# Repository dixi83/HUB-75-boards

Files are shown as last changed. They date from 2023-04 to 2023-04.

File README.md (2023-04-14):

# HUB-75 boards

The HUB-75 boards is a collection of break-out boards (BOBs) for HUB-75 connnectors found on re-purposed FPGA cards such as the 5A-75B and 5A-75E. These cards can be picked up for 10\~20 dollars from China and form an ideal basis for tinkering with FPGAs. Based on these cheap FPGA's a project has been spraked, called Litex-CNC, which aims to repurpose these cards to a cheap CNC controller. CNC-machines normally have field power which is 12\~24V and thus the FPGA cannot direclty be connected to the components of the machine. Therefore a set of break-out boards have been developed for GPIO inputs/outputs, stepgen, encoders, etc.

## Design philosophy
> Why not a hat one might ask? This project offers more flexibility. By combining different break-out can be combined to suit the machine that is being built. A hat also comes with a larger risk in design errors; smaller boards are easier to design, produce and check.

All BOBs will have the same dimensions of 85 mm x 56 mm. This size is equal to that of the Raspberry Pi 4, however the mounting holes are placed on the four corners and thus different from the RPi. Getting the mounting holes at the same location as the RPi made the design much more difficult. Placement of the connectors also hampers stacking these boards on top of each other, so not being to able to stack them on top of a RPi seems permissible.

The outputs of the BOBs will be on the bottom edge (long side). Field power and logic power are provided from the left side of the board. The HUB-75 connectors will be placed on the top of the boards. This makes it easier to route the digital signals and high-power signals separately from each other in the cabinet.

The smalles trace and spacing is 0.2 mm. These boards are designed to be ordered from an online PCB manufacturer. Some desktop milling machines might have the accuracy to create these traces, so you might give it a try when you are feeling lucky. The smallest holes (vias) are 0.3 mm in size.

All components are selected to be hand-solderable. This means that the following minimum sizes SMD components will be used:
- resistors, LED's, capacitors: SMD-1206
- diodes: SOD-123
- FET, transistors: SOT-23

## HUB-75 pinout
Each connector has 6 individual pins (1, 2, 3, 5, 6, and 7) and 8 shared pins (8 through 15). The standard pin-out of a HUB-75 connector is shown below.

| HUB75 pin | Pin | Pin | HUB75 pin |
|---|---|---|---|
| R0 | 1 | 2 | G0 |
| B0 | 3 | 4 | *GND* |
| R1 | 5 | 6 | G1 |
| B1 | 7 | 8 | E |
| A | 9 | 10 | B |
| C | 11 | 12 | D |
| CLK | 13 | 14 | STB |
| OE | 15 | 16 | *GND* |

Each HUB-75 connector will use the individual pins and in special cases one of the shared pins. In the design it should be taken into account that boards which uses the same shared pins might be mutual exclusive when the functions are different (different types of stepgen BOBs can off course be combined.

## Available BOBs
The table below shows the BOBs which are currently available in this repository, along with their status.

| Category  | Name | Description | HUB-75 | Status |
|---|---|---|---|---|
| stepgen | [HUB75-Differential_stepgen](HUB75-Differential_stepgen) | 3 differential stepgen channels, frequency up to 400 kHz | 2 + 0.5 | Prototype-2 ordered |
| GPIO-out  | [HUB75-Sourcing_output](HUB75-Sourcing_output) | 12 channel sourcing output (<1 kHz, 4 A per channel, 4 A total) | 2 | Prototype-2 ordered |
| GPIO-in | [HUB75-Sinking_input](HUB75-Sinking_input) | 12 channel sinking input (< 1 kHz) | 2 | Untested |
| GPIO-in | [HUB75-Sinking_input_screw_terminals](HUB75-Sinking_input_screw_terminals)  | 6 channel sinking input with screw terminals (< 1 kHz) | 2 | Untested |

## Connecting the BOBs to your FPGA
On both the 5A-75B and the 5A-75E the `74HC245T` buffers are hard-wired as outputs. To be able to use the HUB-75 boards which require an input (as seen from the FPGA) some modifications on the board are required. Of both boards different versiosn exist, so the components can be at a different location on your board. Below are the locations of the buffer on a 5A-75B V6.1 (front) and 5A-75E V6.0 (back).

5A-75B V6.1

5A-75E V6.0

Each buffer has 8 channels, while every HUB-75 connector has 6 individual pins. When you replace a buffer you will cahnge the behavior of one HUB-75 connector and partly that of its neighbor. All HUB-75 boards assume that a connector is either fully configured as input or as output. Therefore it is recommended to change the buffers direclty adjacent to each other, so the minimum amount of available connectors (partly input/ouput) are wasted.

The following changes have to be made to the buffers:
* De-solder the `74HC245T` buffer, this buffer cannot be re-used because its pins are not 5 Volt tolerant when `Vcc` is 3.3 Volt.
* Cut the trace to the pin `Vcc` (pin 20) and wire it to a 3.3V source (for example the JTAG-header). If you don't do this, a buffer configure as input will put 5 Volts on the pins of the FPGA, which will definately fry that pin or the whole board.
* Cut the trace to the pin `DIR` (pin 1) and wire it to a GND source to configure the buffer as input.
* Replace the buffer with a buffer with 5V tolerant inputs, such as the `74LVC245` ([datasheet](https://www.ti.com/lit/ds/symlink/sn74lvc245a.pdf)).

After these modifications the board might look a like this (on this particular board a single buffer has been replace, as it is a test-board for LitexCNC).

TODO: picture to be taken

## License 
The boards in this repository are licensed unde Creative Commons BY-NC-SA. This means you are allowed to:
* **Share** — copy and redistribute the material in any medium or format
* **Adapt** — remix, transform, and build upon the material

As long as:
* **Attribution** — You must give appropriate credit, provide a link to the license, and indicate if changes were made. You may do so in any reasonable manner, but not in any way that suggests the licensor endorses you or your use.
* **NonCommercial** — You may not use the material for  commercial purposes. Of course you can use the machine you created or modified using these boards for commercial purposes. 
* **ShareAlike** — If you remix, transform, or build upon the material, you must distribute your contributions under the  same license  as the original.

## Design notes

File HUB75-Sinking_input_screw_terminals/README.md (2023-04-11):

# HUB-75 Sinking input screw terminals
Break-out board with 6 channel sinking input. The FPGA is galvanically separated from field power using opto-couplers.

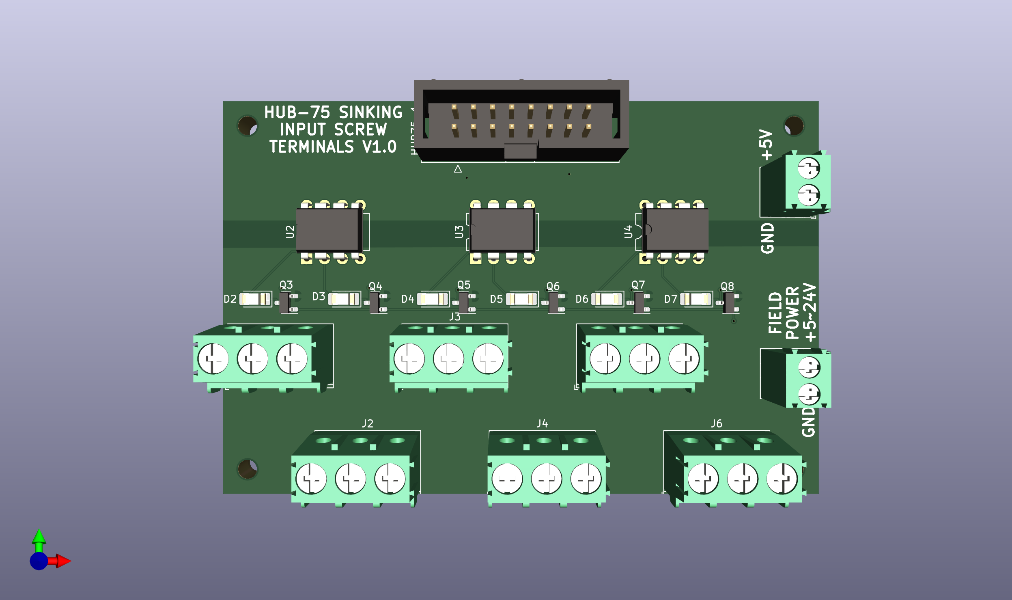
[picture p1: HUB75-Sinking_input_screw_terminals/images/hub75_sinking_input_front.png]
PCB front


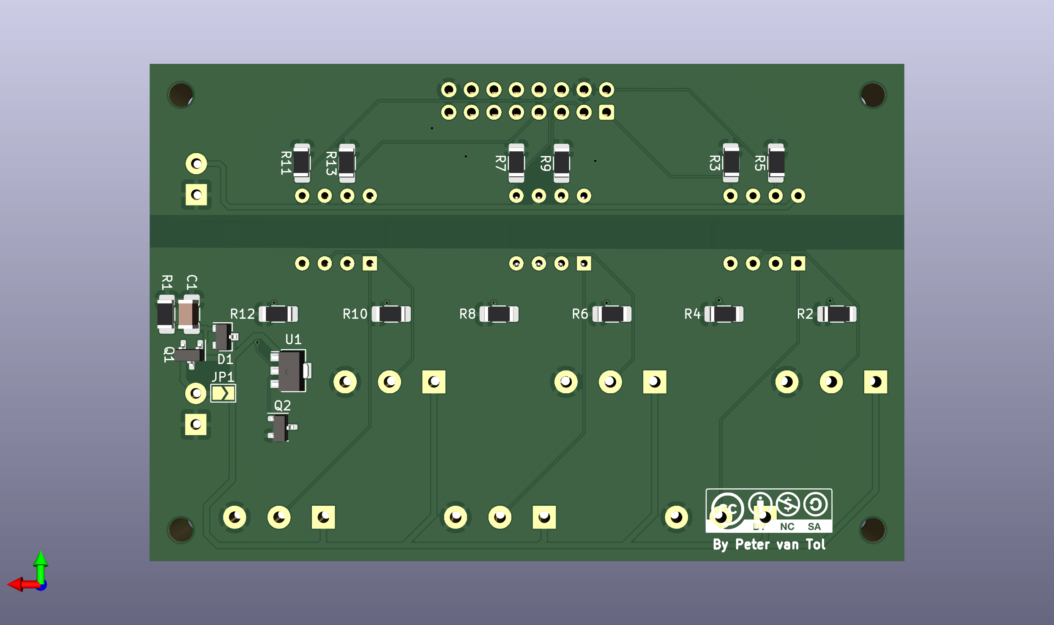
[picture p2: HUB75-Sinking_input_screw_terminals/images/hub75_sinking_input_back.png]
PCB back


## Features

- 1 HUB-75 output connector
- 6 channel sinking output using screw terminals
- 5\~24 V Field power with reverse polarity protection
- indicating LED for each output
- indicated switching frequency 1 kHz

## Applications

- PNP (souring) limit switches
- Momentary push-buttons
- Slow encoders, for example for user input

> **NOTE** <br> The `PC827` optocouplers have a maximum rated frequency of 80 kHz. It is recommended to start at a frequency of 1 kHz and work up from there.

## Example wiring

TODO: example

## Litex-CNC example configuration
Let's assume that the two HUB-745 connectors on this board are connected to J15 and J16 of the FPGA. To configure the pins for output, you can use the configuration-block below as a starting point. Optionaly the pin names can also be set in the configuration, making the HAL clearer.

``` json
{
    ...,
    "gpio_in": [
        {"pin": "j15:0"},
        {"pin": "j15:1"},
        {"pin": "j15:2"},
        {"pin": "j15:4"},
        {"pin": "j15:5"},
        {"pin": "j15:6"}
    ],
    ...
}
```

Alternatively, the BOB can also be used for PWM output. In that case the configuration may look something like below. In this example it is assumed that outputs on J16 are used for three encoders.

``` json
{
    ...,
    "encoders": [
        {  
            "pin_A":"j16:0",
            "pin_B":"j16:1"
        },
        {  
            "pin_A":"j16:2",
            "pin_B":"j16:4"
        },
        {  
            "pin_A":"j16:5",
            "pin_B":"j16:6"
        }
    ],
    ...
}
```

## Bill of materials

The table below gives the bill of materials used for this BOB and an indication of its price. The list is available as public list for the following companies:
* [Reichtelt](https://www.reichelt.de/my/1998173). This is non-affiliate link, I do not earn any money when you order this list from this specific vendor, nor the vendor endorses this project. Reichtelt is a supplyer for Western Europe.

When you order with Mouser or antohter supplier, please share a list here.

| Part. number | Package | Description | Datasheet | Amount | Price*  |
|---|---|---|---|---|---|
| LTV827 | DIP-8 | Dual-channel opto-coupler | | 3 | € 0.31  |
| AO3401A | SOT-23 | P-Channel MOSFET, 30V | | 1 | € 0.25  |
| ZENER 12V | SOT-23 | 12V Zener diode*** | | 1 | € 0.05  |
| 4.7K | SMD 1206  | Resistor, 4.7 kOhm | | 6 | € 0.03  |
| 10K | SMD 1206  | Resistor, 10 kOhm | | 1 | € 0.03  |
| LED | SMD 1206  | LED, green, If > 20 mA | | 6 | € 0.08  |
| CAP 15N | SMD 1206  | Capitor, 15 nF | | 1 | € 0.02  |
| Phoenix_PT-1,5-3-5.0  | - | JST XH conn. 2.5 mm pitch | | 6 | € 0.15  |
| Phoenix_PT-1,5-2-3.5  | - | Screw/spring terminal 2.5 mm pitch | | 2 | € 0.22  |
| BOX 2X8 | - | Box header 2x8, 2.54 mm pitch | | 2 | € 0.16  |
| 2N7002** | SOT-23 | N-Channel MOSFET (current mirror)  | | 7 | € 0.04  |
| CL2N8-G** | SOT-89 | LED-driver 20 mA (current mirror)  | | 1 | € 0.39  |
| R** | SMD 1206  | Resistor, TBD Ohm (alternative) | | 6 | € 0.03  |

**NOTES**: 
1. The price is based on availability in the Netherlands with a single shop for all parts. Parts might be sourced cheaper depending on your location, available sources and the time you want to wait before receiving the components.
2. The components `CL2N8-G` and `2N7002` form a current mirror for driving the status LEDs. This current mirror can be replaced with a fixed resistor `R`, which should be calculated based on the voltage used for Field power.
3. The zener diode is only required when Field Power is >12 Volt for protecting the MOSFETs.

## Known issues

This board does not have any known issues yet.

If you find any issue, please file a bug using GitHub.

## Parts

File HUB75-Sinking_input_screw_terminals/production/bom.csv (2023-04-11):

Source: | C:\Users\Martijn Diks\OneDrive\Documenten\documents\Projects\RatRig Killerbee\ControllerBoard\BOBs\HUB-75-boards-main\HUB75-Sinking_input_screw_terminals\kicad\HUB75-Sinking_input.kicad_sch
Date: | 11-4-2023 18:23:18
Tool: | Eeschema (6.0.9)
Generator: | C:\Program Files\KiCad\6.0\bin\scripting\plugins/bom_csv_grouped_by_value.py
Component Count: | 43
Individual Components:
Item | Qty | Reference(s) | Value | LibPart | Footprint | Datasheet
 |  | C1 | 15nF | Device:C | Capacitor_SMD:C_1206_3216Metric_Pad1.33x1.80mm_HandSolder | ~
 |  | D1 | D_Zener | Device:D_Zener | Diode_SMD:D_SOT-23_ANK | ~
 |  | D2 | LED_Small | Device:LED_Small | LED_SMD:LED_1206_3216Metric_Pad1.42x1.75mm_HandSolder | ~
 |  | D3 | LED_Small | Device:LED_Small | LED_SMD:LED_1206_3216Metric_Pad1.42x1.75mm_HandSolder | ~
 |  | D4 | LED_Small | Device:LED_Small | LED_SMD:LED_1206_3216Metric_Pad1.42x1.75mm_HandSolder | ~
 |  | D5 | LED_Small | Device:LED_Small | LED_SMD:LED_1206_3216Metric_Pad1.42x1.75mm_HandSolder | ~
 |  | D6 | LED_Small | Device:LED_Small | LED_SMD:LED_1206_3216Metric_Pad1.42x1.75mm_HandSolder | ~
 |  | D7 | LED_Small | Device:LED_Small | LED_SMD:LED_1206_3216Metric_Pad1.42x1.75mm_HandSolder | ~
 |  | HUB75-1 | Conn_02x08_Odd_Even | Connector_Generic:Conn_02x08_Odd_Even | Connector_IDC:IDC-Header_2x08_P2.54mm_Vertical | ~
 |  | J1 | Conn_01x03_Male | Connector:Conn_01x03_Male | Connector_JST:JST_XH_B3B-XH-A_1x03_P2.50mm_Vertical | ~
 |  | J2 | Conn_01x03_Male | Connector:Conn_01x03_Male | Connector_JST:JST_XH_B3B-XH-A_1x03_P2.50mm_Vertical | ~
 |  | J3 | Conn_01x03_Male | Connector:Conn_01x03_Male | Connector_JST:JST_XH_B3B-XH-A_1x03_P2.50mm_Vertical | ~
 |  | J4 | Conn_01x03_Male | Connector:Conn_01x03_Male | Connector_JST:JST_XH_B3B-XH-A_1x03_P2.50mm_Vertical | ~
 |  | J5 | Conn_01x03_Male | Connector:Conn_01x03_Male | Connector_JST:JST_XH_B3B-XH-A_1x03_P2.50mm_Vertical | ~
 |  | J6 | Conn_01x03_Male | Connector:Conn_01x03_Male | Connector_JST:JST_XH_B3B-XH-A_1x03_P2.50mm_Vertical | ~
 |  | JP1 | Jumper_2_Open | Jumper:Jumper_2_Open | Jumper:SolderJumper-2_P1.3mm_Open_TrianglePad1.0x1.5mm | ~
 |  | PWR1 | Screw_Terminal_01x02 | Connector:Screw_Terminal_01x02 | TerminalBlock_Phoenix:TerminalBlock_Phoenix_PT-1,5-2-3.5-H_1x02_P3.50mm_Horizontal | ~
 |  | PWR2 | Screw_Terminal_01x02 | Connector:Screw_Terminal_01x02 | TerminalBlock_Phoenix:TerminalBlock_Phoenix_PT-1,5-2-3.5-H_1x02_P3.50mm_Horizontal | ~
 |  | Q1 | AO3401A | Transistor_FET:AO3401A | Package_TO_SOT_SMD:SOT-23 | http://www.aosmd.com/pdfs/datasheet/AO3401A.pdf
 |  | Q2 | 2N7002 | Transistor_FET:2N7002 | Package_TO_SOT_SMD:SOT-23 | https://www.onsemi.com/pub/Collateral/NDS7002A-D.PDF
 |  | Q3 | 2N7002 | Transistor_FET:2N7002 | Package_TO_SOT_SMD:SOT-23 | https://www.onsemi.com/pub/Collateral/NDS7002A-D.PDF
 |  | Q4 | 2N7002 | Transistor_FET:2N7002 | Package_TO_SOT_SMD:SOT-23 | https://www.onsemi.com/pub/Collateral/NDS7002A-D.PDF
 |  | Q5 | 2N7002 | Transistor_FET:2N7002 | Package_TO_SOT_SMD:SOT-23 | https://www.onsemi.com/pub/Collateral/NDS7002A-D.PDF
 |  | Q6 | 2N7002 | Transistor_FET:2N7002 | Package_TO_SOT_SMD:SOT-23 | https://www.onsemi.com/pub/Collateral/NDS7002A-D.PDF
 |  | Q7 | 2N7002 | Transistor_FET:2N7002 | Package_TO_SOT_SMD:SOT-23 | https://www.onsemi.com/pub/Collateral/NDS7002A-D.PDF
 |  | Q8 | 2N7002 | Transistor_FET:2N7002 | Package_TO_SOT_SMD:SOT-23 | https://www.onsemi.com/pub/Collateral/NDS7002A-D.PDF
 |  | R1 | 10K | Device:R | Resistor_SMD:R_1206_3216Metric_Pad1.30x1.75mm_HandSolder | ~
 |  | R2 | R | Device:R | Resistor_SMD:R_1206_3216Metric_Pad1.30x1.75mm_HandSolder | ~
 |  | R3 | 4.7K | Device:R | Resistor_SMD:R_1206_3216Metric_Pad1.30x1.75mm_HandSolder | ~
 |  | R4 | R | Device:R | Resistor_SMD:R_1206_3216Metric_Pad1.30x1.75mm_HandSolder | ~
 |  | R5 | 4.7K | Device:R | Resistor_SMD:R_1206_3216Metric_Pad1.30x1.75mm_HandSolder | ~
 |  | R6 | R | Device:R | Resistor_SMD:R_1206_3216Metric_Pad1.30x1.75mm_HandSolder | ~
 |  | R7 | 4.7K | Device:R | Resistor_SMD:R_1206_3216Metric_Pad1.30x1.75mm_HandSolder | ~
 |  | R8 | R | Device:R | Resistor_SMD:R_1206_3216Metric_Pad1.30x1.75mm_HandSolder | ~
 |  | R9 | 4.7K | Device:R | Resistor_SMD:R_1206_3216Metric_Pad1.30x1.75mm_HandSolder | ~
 |  | R10 | R | Device:R | Resistor_SMD:R_1206_3216Metric_Pad1.30x1.75mm_HandSolder | ~
 |  | R11 | 4.7K | Device:R | Resistor_SMD:R_1206_3216Metric_Pad1.30x1.75mm_HandSolder | ~
 |  | R12 | R | Device:R | Resistor_SMD:R_1206_3216Metric_Pad1.30x1.75mm_HandSolder | ~
 |  | R13 | 4.7K | Device:R | Resistor_SMD:R_1206_3216Metric_Pad1.30x1.75mm_HandSolder | ~
 |  | U1 | CL2N8-G | Driver_LED:HV9921N8-G | Package_TO_SOT_SMD:SOT-89-3 | https://cdn-reichelt.de/documents/datenblatt/A200/CL2_DS.pdf
 |  | U2 | LTV-827 | Isolator:LTV-827 | Package_DIP:DIP-8_W7.62mm | http://optoelectronics.liteon.com/upload/download/DS-70-96-0016/LTV-8X7%20series%20201610%20.pdf
 |  | U3 | LTV-827 | Isolator:LTV-827 | Package_DIP:DIP-8_W7.62mm | http://optoelectronics.liteon.com/upload/download/DS-70-96-0016/LTV-8X7%20series%20201610%20.pdf
 |  | U4 | LTV-827 | Isolator:LTV-827 | Package_DIP:DIP-8_W7.62mm | http://optoelectronics.liteon.com/upload/download/DS-70-96-0016/LTV-8X7%20series%20201610%20.pdf
Collated Components:
Item | Qty | Reference(s) | Value | LibPart | Footprint | Datasheet
1 | 1 | C1 | 15nF | Device:C | Capacitor_SMD:C_1206_3216Metric_Pad1.33x1.80mm_HandSolder | ~
2 | 1 | D1 | D_Zener | Device:D_Zener | Diode_SMD:D_SOT-23_ANK | ~
3 | 6 | D2, D3, D4, D5, D6, D7 | LED_Small | Device:LED_Small | LED_SMD:LED_1206_3216Metric_Pad1.42x1.75mm_HandSolder | ~
4 | 1 | HUB75-1 | Conn_02x08_Odd_Even | Connector_Generic:Conn_02x08_Odd_Even | Connector_IDC:IDC-Header_2x08_P2.54mm_Vertical | ~
5 | 6 | J1, J2, J3, J4, J5, J6 | Conn_01x03_Male | Connector:Conn_01x03_Male | Connector_JST:JST_XH_B3B-XH-A_1x03_P2.50mm_Vertical | ~
6 | 1 | JP1 | Jumper_2_Open | Jumper:Jumper_2_Open | Jumper:SolderJumper-2_P1.3mm_Open_TrianglePad1.0x1.5mm | ~
7 | 2 | PWR1, PWR2 | Screw_Terminal_01x02 | Connector:Screw_Terminal_01x02 | TerminalBlock_Phoenix:TerminalBlock_Phoenix_PT-1,5-2-3.5-H_1x02_P3.50mm_Horizontal | ~
8 | 1 | Q1 | AO3401A | Transistor_FET:AO3401A | Package_TO_SOT_SMD:SOT-23 | http://www.aosmd.com/pdfs/datasheet/AO3401A.pdf
9 | 7 | Q2, Q3, Q4, Q5, Q6, Q7, Q8 | 2N7002 | Transistor_FET:2N7002 | Package_TO_SOT_SMD:SOT-23 | https://www.onsemi.com/pub/Collateral/NDS7002A-D.PDF
10 | 1 | R1 | 10K | Device:R | Resistor_SMD:R_1206_3216Metric_Pad1.30x1.75mm_HandSolder | ~
11 | 6 | R2, R4, R6, R8, R10, R12 | R | Device:R | Resistor_SMD:R_1206_3216Metric_Pad1.30x1.75mm_HandSolder | ~
12 | 6 | R3, R5, R7, R9, R11, R13 | 4.7K | Device:R | Resistor_SMD:R_1206_3216Metric_Pad1.30x1.75mm_HandSolder | ~
13 | 1 | U1 | CL2N8-G | Driver_LED:HV9921N8-G | Package_TO_SOT_SMD:SOT-89-3 | https://cdn-reichelt.de/documents/datenblatt/A200/CL2_DS.pdf
14 | 3 | U2, U3, U4 | LTV-827 | Isolator:LTV-827 | Package_DIP:DIP-8_W7.62mm | http://optoelectronics.liteon.com/upload/download/DS-70-96-0016/LTV-8X7%20series%20201610%20.pdf

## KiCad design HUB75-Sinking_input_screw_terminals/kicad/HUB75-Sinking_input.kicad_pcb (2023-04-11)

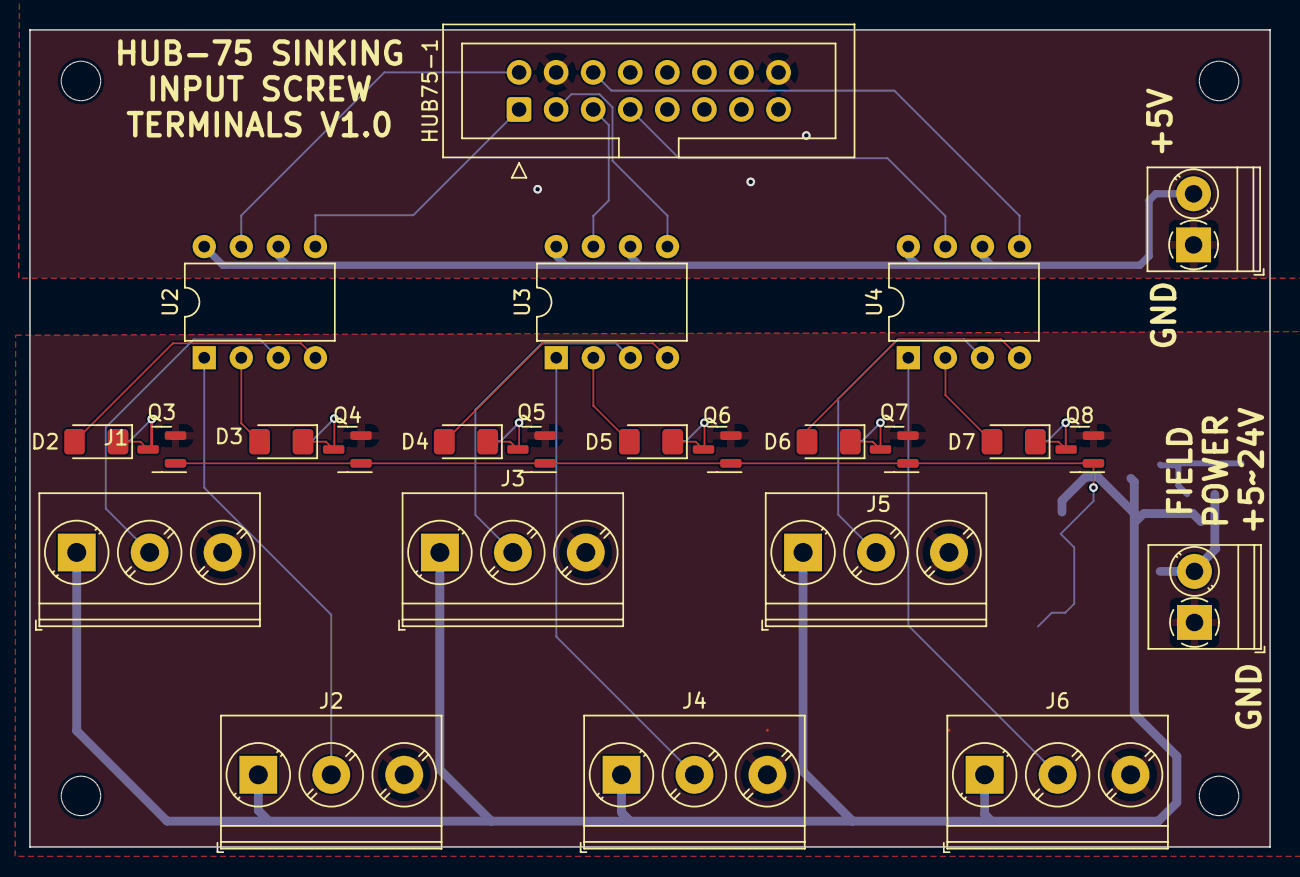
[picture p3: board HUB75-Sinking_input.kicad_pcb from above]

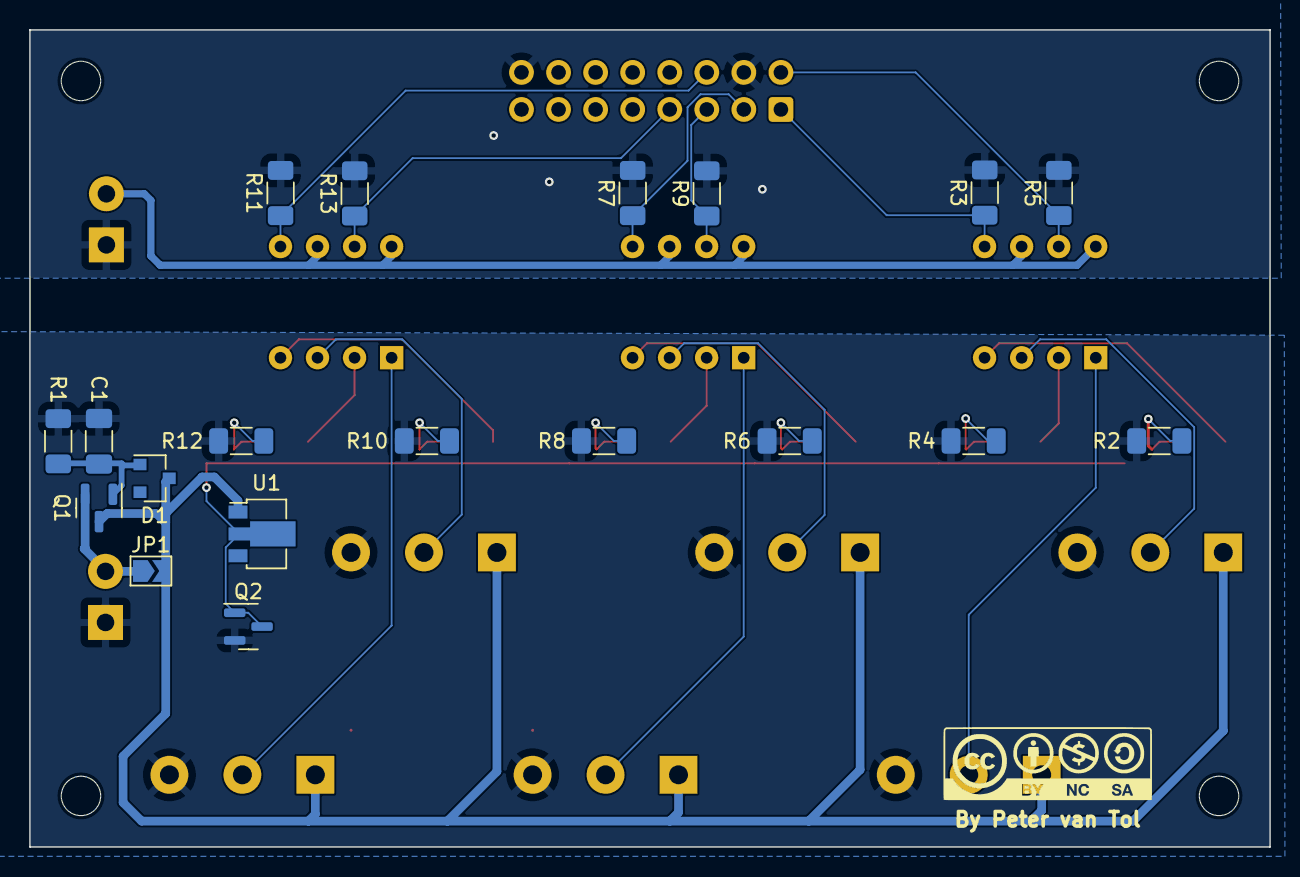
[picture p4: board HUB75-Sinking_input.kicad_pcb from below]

Board: 2 copper layers, 85.0 x 56.0 mm, 47 parts (19 on the bottom side), 31 nets.

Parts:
C1: 15nF; C_1206_3216Metric_Pad1.33x1.80mm_HandSolder
D1: D_Zener; D_SOT-23_ANK
D2, D3, D4, D5, D6, D7: LED_Small; LED_1206_3216Metric_Pad1.42x1.75mm_HandSolder
HOLE1, HOLE2, HOLE3, HOLE4: MountingHole_2.7mm_M2.5_DIN965
HUB75-1: Conn_02x08_Odd_Even; IDC-Header_2x08_P2.54mm_Vertical
J1, J2, J3, J4, J5: Conn_01x03_Male; TerminalBlock_Phoenix_PT-1,5-3-5.0-H_1x03_P5.00mm_Horizontal
J6: TerminalBlock_Phoenix:TerminalBlock_Phoenix_PT-1,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; TerminalBlock_Phoenix_PT-1,5-3-5.0-H_1x03_P5.00mm_Horizontal
JP1: Jumper_2_Open; SolderJumper-2_P1.3mm_Open_TrianglePad1.0x1.5mm
PWR1, PWR2: Screw_Terminal_01x02; TerminalBlock_Phoenix_PT-1,5-2-3.5-H_1x02_P3.50mm_Horizontal
Q1: AO3401A; SOT-23
Q2, Q3, Q4, Q5, Q6, Q7, Q8: 2N7002; SOT-23
R1: 10K; R_1206_3216Metric_Pad1.30x1.75mm_HandSolder
R2, R4, R6, R8, R10, R12: R; R_1206_3216Metric_Pad1.30x1.75mm_HandSolder
R3, R5, R7, R9, R11, R13: 4.7K; R_1206_3216Metric_Pad1.30x1.75mm_HandSolder
U1: CL2N8-G; SOT-89-3
U2, U3, U4: LTV-827; DIP-8_W7.62mm

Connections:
+5V: PWR2.2, U2.6, U2.8, U3.6, U3.8, U4.6, U4.8
CUR_MIRROR: Q2.1 (G), Q2.3 (D), Q3.1 (G), Q4.1 (G), Q5.1 (G), Q6.1 (G), Q7.1 (G), Q8.1 (G), U1.2 (GND)
GND: HUB75-1.4, HUB75-1.16, PWR2.1, R3.2, R5.2, R7.2, R9.2, R11.2, R13.2
GNDD: C1.2, J1.3, J2.3, J3.3, J4.3, J5.3, J6.3, PWR1.1, Q2.2 (S), Q3.2 (S), Q4.2 (S), Q5.2 (S), Q6.2 (S), Q7.2 (S), Q8.2 (S), R1.2, R2.1, R4.1, R6.1, R8.1, R10.1, R12.1
GPIO1-1: HUB75-1.1, R3.1, U2.5
GPIO1-2: HUB75-1.2, R5.1, U2.7
GPIO1-3: HUB75-1.3, R7.1, U3.5
GPIO1-4: HUB75-1.5, R9.1, U3.7
GPIO1-5: HUB75-1.6, R11.1, U4.5
GPIO1-6: HUB75-1.7, R13.1, U4.7
unnamed: C1.1, D1.2 (A), Q1.1 (G), R1.1
unnamed: D2.1 (K), Q3.3 (D), R2.2
unnamed: D2.2 (A), U2.4
unnamed: D3.1 (K), Q4.3 (D), R4.2
unnamed: D3.2 (A), U2.2
unnamed: D4.1 (K), Q5.3 (D), R6.2
unnamed: D4.2 (A), U3.4
unnamed: D5.1 (K), Q6.3 (D), R8.2
unnamed: D5.2 (A), U3.2
unnamed: D6.1 (K), Q7.3 (D), R10.2
unnamed: D6.2 (A), U4.4
unnamed: D7.1 (K), Q8.3 (D), R12.2
unnamed: D7.2 (A), U4.2
unnamed: J1.2, U2.3
unnamed: J2.2, U2.1
unnamed: J3.2, U3.3
unnamed: J4.2, U3.1
unnamed: J5.2, U4.3
unnamed: J6.2, U4.1
unnamed: JP1.1 (A), PWR1.2, Q1.2 (S)
VDD: D1.1 (K), J1.1, J2.1, J3.1, J4.1, J5.1, J6.1, JP1.2 (B), Q1.3 (D), U1.1 (VDD)

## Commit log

2023-04-11 Added screw terminal BOB
2023-04-11 add Input board with screw terminals
    [HUB75-Sinking_input.kicad_pcb, HUB75-Sinking_input.kicad_sch, optocoupler_channel.kicad_sch]
2023-04-11 after the last edits
    [HUB75-Sinking_input.kicad_pcb, bom.csv]
2023-04-14 DIR pin is 1

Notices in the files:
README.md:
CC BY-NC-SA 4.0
